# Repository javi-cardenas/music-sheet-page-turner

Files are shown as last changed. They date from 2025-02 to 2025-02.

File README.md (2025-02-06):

# Sheet Music Page Turner

This page-turning device was designed with reading and multitasking in mind. While devices for eBooks already exist, our solution primarily aimed to provide a cheaper hands-free alternative for physical sheet music books.

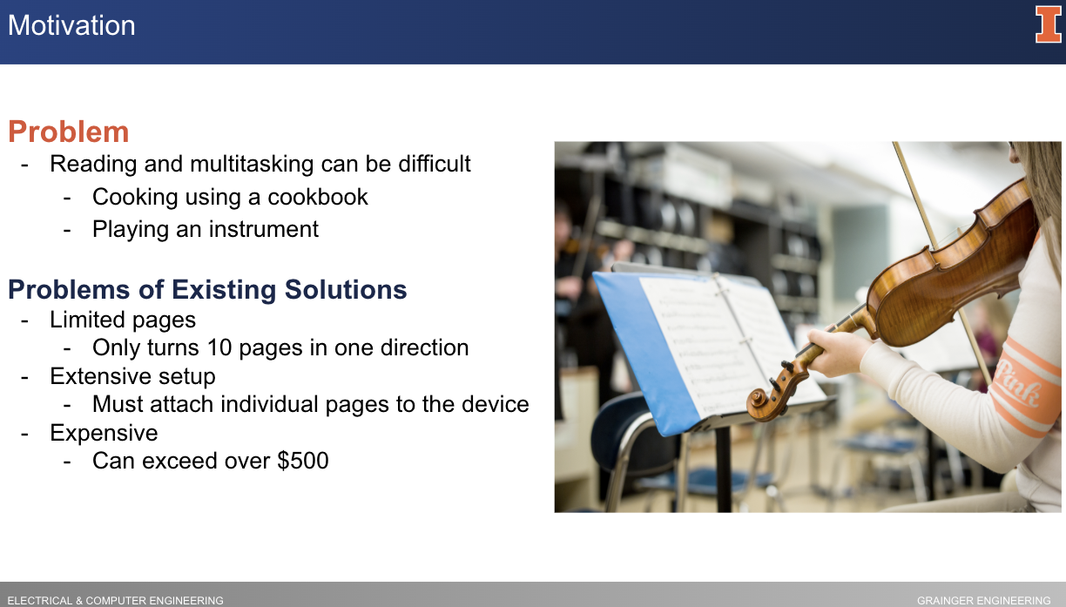
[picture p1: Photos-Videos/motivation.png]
Problem


<div align="center">
  <h2>Minimum Viable Product</h2>
</div>

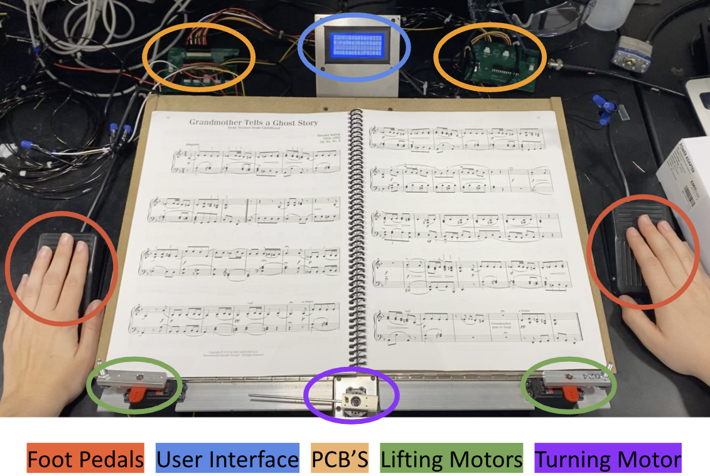
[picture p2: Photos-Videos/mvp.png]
Minimum Viable Product


Our page turner uses two foot pedals as input and three servo motors to turn pages forward or backward. The servo motors are attached to the base of a wooden stand and a liquid crystal display (LCD) is mounted to a metal enclosure.

Ultimately, the device was successfully able to turn pages in both directions, consecutively turn up to 10 pages in a row, and digitally track the number of pages the user turned.

**Note:** Feel free to take any inspiration, but this code was not intended to be cloned and deployed. As such, I do not provide support or guidance for this.

<div align="center">
  <h2>Software Flow Chart</h2>
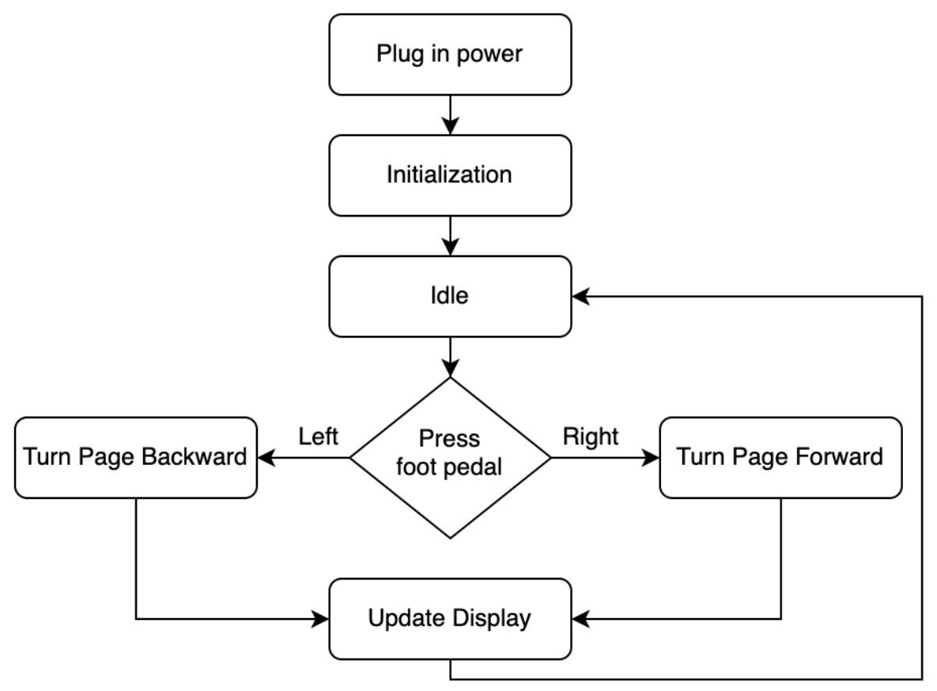
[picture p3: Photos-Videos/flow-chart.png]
Software Flow Chart
  
</div>

<div align="center">
  <h2>Block Diagram</h2>
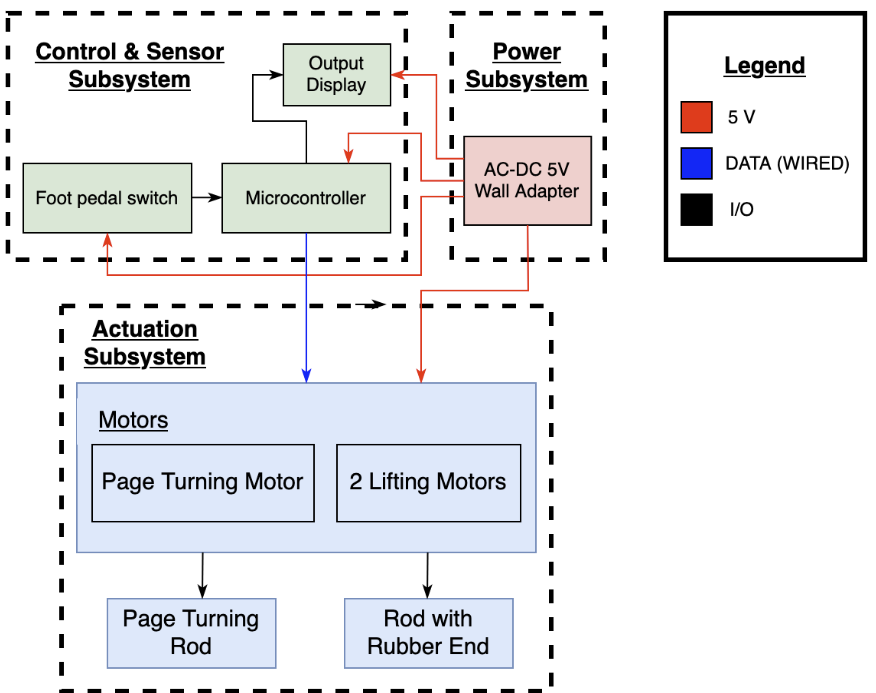
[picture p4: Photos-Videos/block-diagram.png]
Block Diagram
  
</div>

<div align="center">
  <h2>Circuit Schematic</h2>
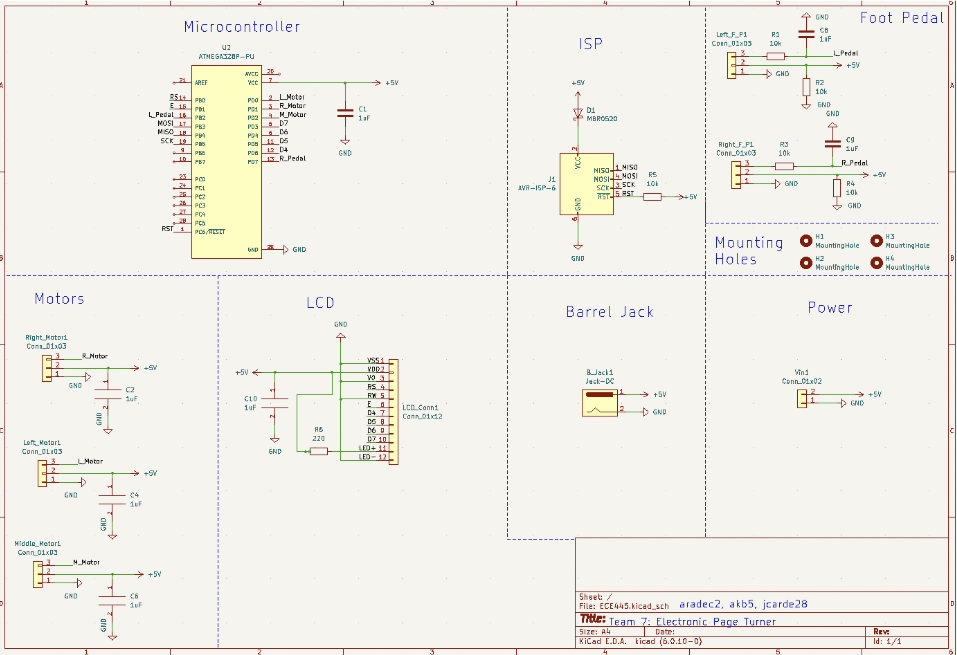
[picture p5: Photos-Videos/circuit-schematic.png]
Circuit Schematic
  
</div>

<div align="center">
  <h2>Printable Circuit Board (PCB) Diagram</h2>
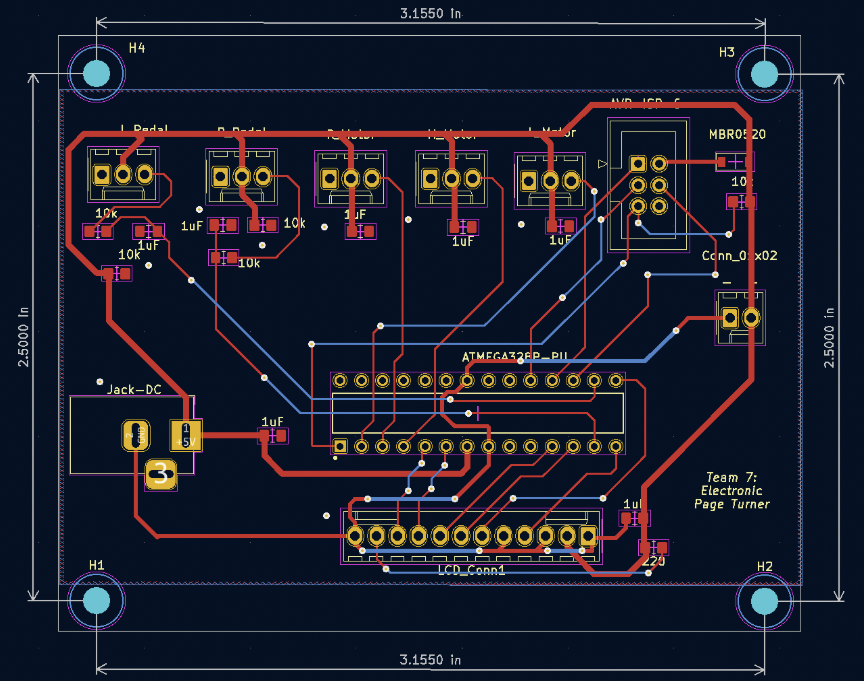
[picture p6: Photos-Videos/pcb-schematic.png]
Printable Circuit Board (PCB) Diagram
  
</div>

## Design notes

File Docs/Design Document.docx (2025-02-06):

ECE 445 Senior Design

Design Document

Electronic Page Turner

Team No. 7

Adia Radecka

(aradec2@illinois.edu)

Alyssa Bradshaw

(akb5@illinois.edu)

Javi Cardenas

(jcarde28@illinois.edu)

TA: Raman Singh

Professor: Viktor Gruev

March 31, 2023

Table of Contents

1. Introduction 2

1.1 Problem 2

1.2 Solution 3

1.3 High-Level Requirements 3

2. Design 6

2.1 Block Diagram 6

2.2 Subsystem Overview 6

2.2.1 Power Subsystem 6

2.2.2 Control & Sensor Subsystem 7

2.2.3 Actuation Subsystem 8

2.3 Subsystem Requirements 9

2.2.1 Power Subsystem 9

2.2.2 Control & Sensor Subsystem 9

2.2.3 Actuation Subsystem 9

2.4 Tolerance Analysis 9

3. Cost & Schedule 10

3.1 Cost Analysis 10

3.2 Schedule 11

4. Ethics & Safety 13

4.1 Ethics 13

4.2 Safety 13

5. References 14

# 1. Introduction

## 1.1 Problem

When reading a book, manual page-turning is a crucial requirement. This simple task can inconvenience those wishing to multitask while reading. A prime example occurs when a musician must stop playing their instrument to turn the sheet music when practicing or performing music. Another example is when cooking and using a cookbook; one may not have free or clean hands to turn the pages. Furthermore, a group to consider is those with disabilities who cannot physically turn a book's pages [1]. These are just a few examples of electronic page-turners’ usefulness, but not many exist. Those that do are generally expensive and typically designed for electronic tablet reading. Another issue with existing page-turners for physical books is that they are made for a limited number of pages and can only turn them in one direction. They also require a lengthy setup to attach each page to the device, which is an issue for those wanting to use a book with more pages than the device can handle.

## 1.2 Solution

To solve this problem, our team aims to create a hands-free electronic page-turner that functions with a foot pedal. The device uses two foot pedal switches to turn a page forward or backward. When the foot pedal is pressed, the control system communicates with the motors to start turning a page. A rubber tip attached to the end of a motor is used to lift a single page at a time. A rod connected to another motor will sweep underneath the raised page, causing it to turn to the next page. Our solution is unique because the device does not require extensive setup and can go through all the pages in a physical book in both directions.

## 1.3 Visual Aid

We provide a pictorial representation of our solution in Figure 1. The main components attached to the book stand will be the motors and a Liquid Crystal Display (LCD).

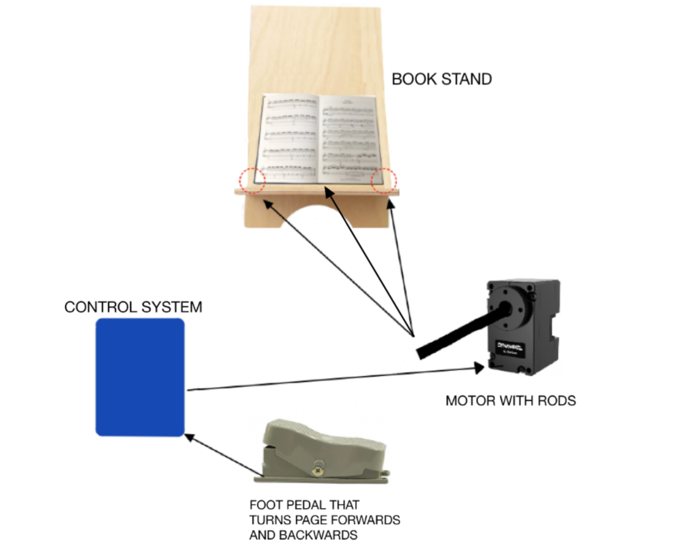
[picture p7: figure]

Figure 1: Visual Aid

## 1.4 High-Level Requirements

For our solution to be considered successful, it must achieve the following three goals:

- The device must be able to turn one page within 5 seconds ± 2 seconds. This motion should be repeatable for turning a page backward.
- The device must be able to turn at least ten consecutive pages, with 95% ± 5% accuracy, and take at most 1 minute ± 10 seconds when the foot pedal is pressed consecutively.
- The device must be able to store the total number of pages turned in a single sitting, with 95% ± 5% accuracy, and display this information to the reader.

# 2. Design

## 2.1 Physical Design

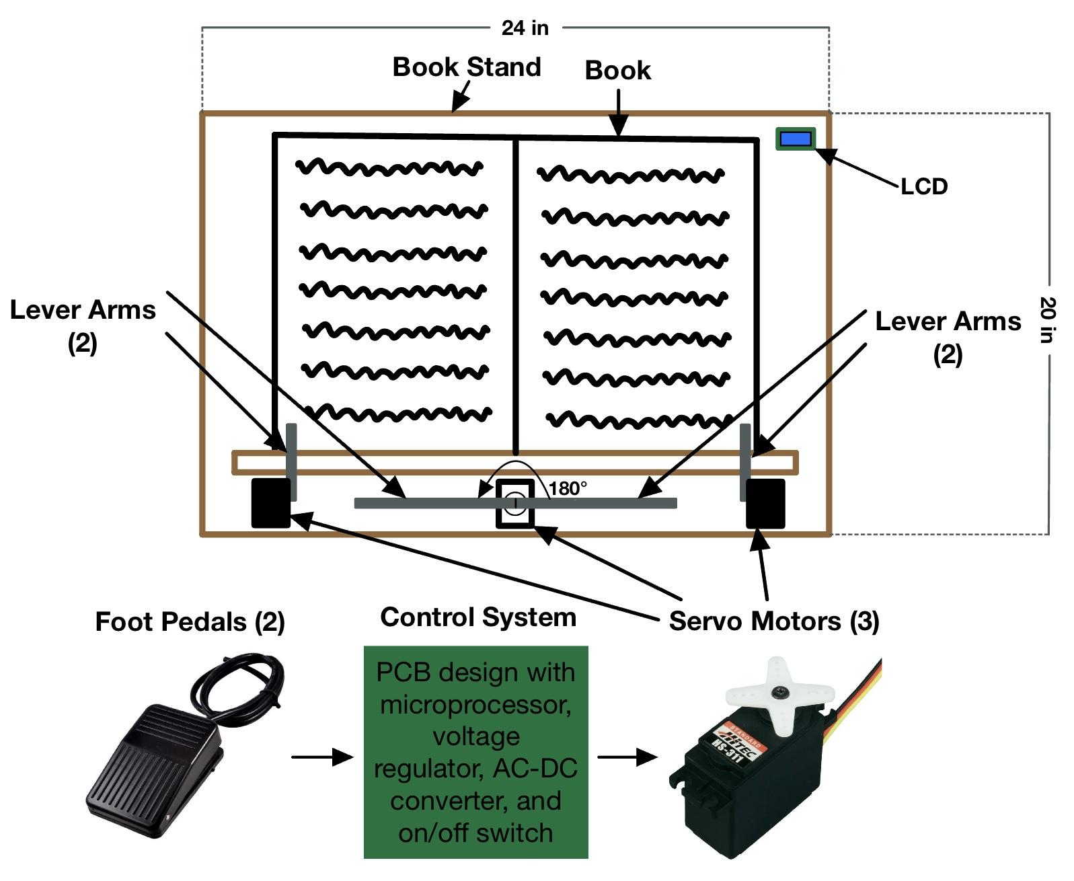
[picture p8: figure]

Figure 2: Physical Design

This physical design consists of two foot pedal switches, three servo motors, a physical stand to hold the book, a PCB, and an LCD. The input to our device is two foot pedals, and the physical page-turning and LCD act as the output. The LCD keeps track of the number of pages turned forward. The system uses a 5V wall-power adapter to power all its components. The PCB comprises the microcontroller and headers to connect the pedals, motors, and LCD. Two servo motors with rods containing rubber tips at their ends must be located by the corners of the book stand to raise a single page vertically. The center servo motor includes a long rod to sweep underneath the raised page.

## 2.2 Block Diagram

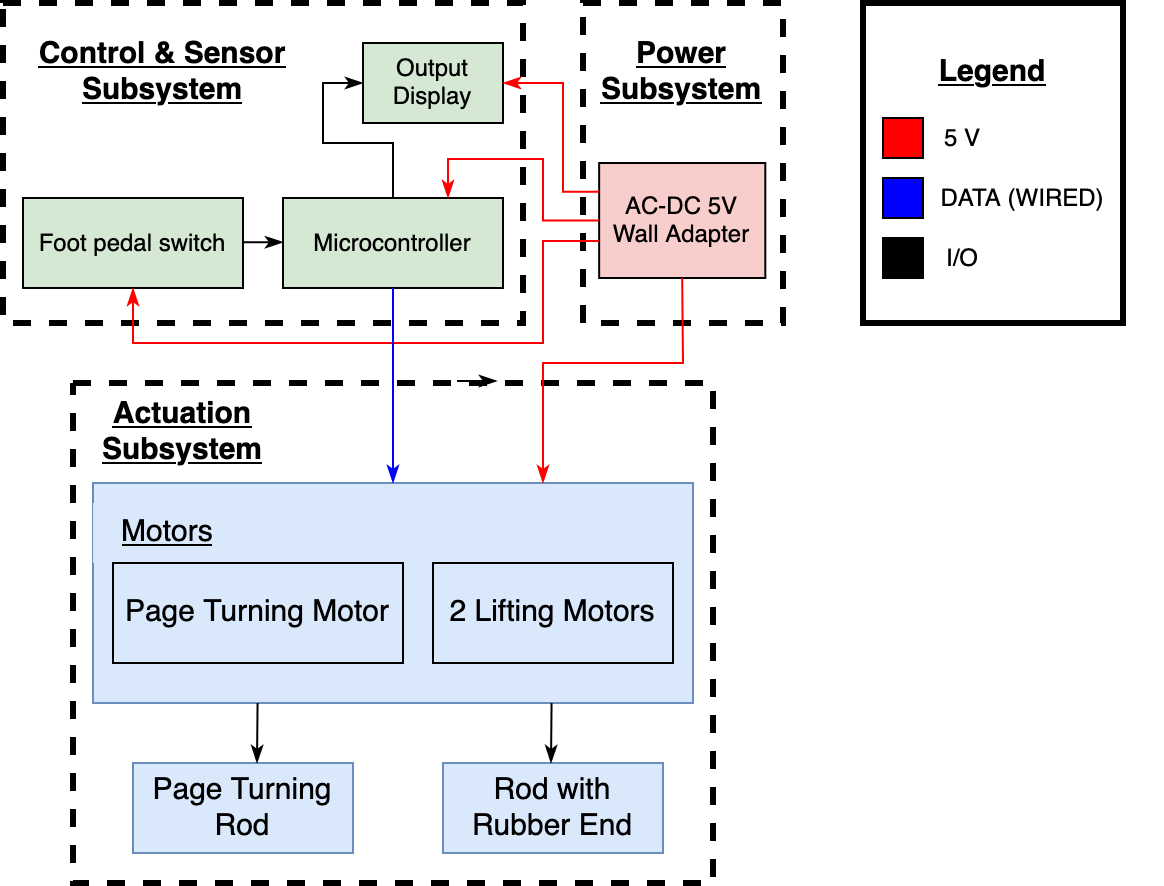
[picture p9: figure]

Figure 3: Block Diagram

## 2.3 Subsystem Overview

Our design is divided into three subsystems: Power, Control & Sensor, and Actuation subsystems.

### 2.3.1 Power Subsystem

The power subsystem handles sending power to the rest of the components in the other two subsystems. The power subsystem includes a 5V wall-power adapter that converts from AC-DC, supplying a steady 5V to the rest of the subsystems.

### 2.3.2 Control & Sensor Subsystem

The control and sensor subsystem contains the microcontroller and sensors needed to move the motors. This includes the ATMEGA328P microcontroller, two foot pedal switches, and an LCD. When a foot pedal is pressed, a signal is sent to the microcontroller, determining whether a page is turned forward or backward. The microcontroller then sends a signal to turn on the correct servo motors. The LCD keeps track of the number of pages turned forward.

### 2.3.3 Actuation Subsystem

Two servo motors will lift a single page vertically, the left and right pages, respectively. Attached to the end of each lifting motor will be a short rod with a rubber tip; these motors will be located at the bottom corners of each page. The remaining servo motor will turn the page forward or backward. This page-turning motor will be located by the center of the book stand. Attached to the page-turning motor will be a long rod that rests below the bottom of the book. When the foot pedal is pressed, and the microcontroller processes and sends the signal, the page-turning process will start. First, the lifting motor will move from 0° to 45°, next the center motor will move from 0° to 90°, then the lifting motor will return to its starting position, and finally, the center motor will move to 180° causing the raised page to turn to the next page.

## 2.4 Subsystem Requirements

The requirements for each of our subsystems.

### 2.4.1 Power Subsystem

The power subsystem handles sending power to the rest of the components in the other two subsystems.

Requirements | Verification
- Must have a 5V wall adapter that plugs into a wall outlet. - All components must be supplied with 5 V ± 5%, when the devices are idle and when active. | - Use a multimeter to check that the wall adapter’s barrel jack is supplying a steady 5V ± 5%. - While the device is turned on, measure the voltage across each device using an oscilloscope. Repeat this process when a foot pedal is pressed.

### 2.4.2 Control & Sensor Subsystem

The control and sensor subsystem contains the microcontroller and sensors needed to move the motors. The foot pedal sensor must be able to send a signal when pressed to the microcontroller. The microcontroller must then communicate with the motors to begin turning pages.

Requirements | Verification
- When the left foot pedal is pressed, the corresponding motors to turn a page backward should rotate. When the right foot pedal is pressed, the corresponding motors to turn a page forward should rotate. - LCD Display must track the number of pages turned forward. | - Test the situation where the foot pedal is not pressed. Ensure that the motors do not rotate. - Test the situation where the foot pedal is pressed. Ensure that the lifting motors rotate 0°-45°-0° and the center motor rotates 0°-90°-180°. - When a page is turned forward, the count should increase by 1. If a page is turned backward, the count should decrease by 1.

### 2.4.3 Actuation Subsystem

The actuation subsystem handles the mechanical work of turning the page and includes three servo motors. The motors must successfully lift a page and then turn that page over. This motion must be repeatable for forwards and backwards page turning.

Requirement | Verification

- The servo motors must create negligible backwards EMF.
- The force of the motors should not be enough to cause tearing or damage to the books pages.
- Use an oscilloscope to plot the voltage of a motor when idle and when active. If the voltage spike is 1V ± 0.5V we can consider the backwards EMF from the motor negligible. Otherwise, we will add more capacitors and diodes to prevent negatively impacting the other hardware in our device.
- Using a singular lifting motor, run 10 trials to test how the force and speed required to lift one page. Tune the parameters in software accordingly.
- Using the sweeping motor, run 10 trials to test the force and speed required to lift one page. Tune the parameters in software accordingly. The slowest speed required to turn a page will be chosen for safety.

## 2.5 Tolerance Analysis

A crucial part of our project's success is the motors to lift a single page and the center motor to flip the page. We must consider the thickness of a book and how far along into the book we are for the lifting motors to hold a page vertically. For testing, we will be using a music sheet book with the following dimensions: 9 x 0.24 x 12 inches. The lifting motors must reach low enough to grab the very last page of the book, which would be at 0.0025 inches. We determined that the page must be lifted one inch to provide the sweeping rod attached to the center motor enough space to flip the page. Therefore a singular page must be displaced 45°, with respect to, the book if using a one inch rod to lift the page as shown in Equation 1.

Θ_(page, max) =tan^(-1) (1/1)=45°=0.785 rad

Equation 1: Angular displacement for a 1 in. rod attached to lifting motor

Θ_(page, min) =tan^(-1) (1/3)=18.4°=0.321 rad

Equation 2: Angular displacement for a 3 in. rod attached to lifting motor

Θ_(sweep) =180°=3.14 rad

Equation 3: Angular displacement for sweeping rod attached to center motor

Additionally, two of our high-level requirements involve time. More specifically, the time it takes to flip a single page and to turn ten pages consecutively. According to the datasheet for the motors, the maximum torque each can provide is 5.5 kg/cm = 0.053937 Nm, as shown in Equation 4. Ideally, each motor will receive 600 mW of power, as shown in Equation 5. By finding the maximum angular velocity, in Equation 6, the time it takes for each motor to complete its angular displacement can be calculated as shown in Equation 7. This process will ideally take 423.62 ms (2 X 70.603 + 282.41 ms). While these calculations are under ideal conditions, realistically, we can expect the process to take about 1 second. We also have to consider going too fast may cause physical damage to the book’s pages, which we plan to avoid. Furthermore, the time delay for signals from the foot pedal and microcontroller will require additional time. Therefore our given estimate in the high-level requirements is a reasonable baseline.

τ_(motor) =5.5 kg/cm = 0.053937 Nm

Equation 4: Maximum torque provided in motor datasheet

P_(motor) =I_(motor) V_(motor)

P_(motor) =0.1 [A] ×6 [V] = 0.6 W

Equation 5: Maximum power provided to each motor

P=τω→ω = P÷τ

ω=0.6 [W] ÷0.053937 [Nm] = 11.124 rad/s

Equation 6: Maximum angular velocity for each motor

t_(Θ_(page, max)) = (1 s)/(11.124 rad)×0.785 rad =70.603 ms

t_(Θ_(page, min)) = (1 s)/(11.124 rad)×0.321 rad =28.924 ms

t_(Θ_(sweep)) = (1 s)/(11.124 rad)×3.14 rad =282.41 ms

Equation 7: Time required for each motor to reach their angular displacement

# 3. Cost & Schedule

## 3.1 Cost Analysis

Production of this device is estimated at 30 hours per week over 15 weeks distributed amongst three people. The three of us are electrical engineering majors, and based on our current job offers, the average pay is $40 per hour. Based on this hourly rate, the estimated labor cost for this initial design is $18,000.

Below we have included a table to breakdown the cost of all parts required for the initial design. Based on these numbers we estimate a cost of $129.57 for all required components.

Part | Part Number | Unit Price | Quantity | Total
Microcontroller | ATMEGA328P-PU | | 1
Foot Pedal | n/a | $10.43 | 2 | $20.86
Servo Motor | HS-311 | $14.76 | 3 | $44.28
PCB Manufacture | n/a | $30.00 | 1 | $30.00
On/Off Switch | JS202011CQN | $0.60 | 1 | $0.60
AC to DC Converter | UCC28610DR | $1.65 | 1 | $1.65
Barrel Jack | PJ-102AH | $0.82 | 1 | $0.82
Power Plug | PP3-002A | $1.44 | 1 | $1.44
Linear Regulator | LM117MP | $1.70 | 1 | $1.69
ISP Header | 1597-114020164-ND | $2.80 | 1 | $2.80
3 Pin Header | WM4201-ND | $0.27 | 3 | $0.81
LCD Display | 2632-C162A-BW-LW65-ND | $6.27 | 1 | $6.27
10k Resistor | 2197-294-10-RC-ND | $0.15 | 3 | $0.45
1uF Capacitor | 478-1836-ND | $0.82 | 3 | $2.46
3 pin MTA100 connector | A19470-ND | $0.23 | 3 | $0.69
3D Printed Motor Rods | N/a | $1.00 | 3 | $3.00
Total Cost | | | | $129.57

Table 1: Total Cost of Required Components

## 3.2 Schedule

- Week of 02/20; Week 6

Design Document, Team Contract, Revise Proposal, Work on PCB Design in office hours, Make design review presentation

- Week of 02/27; Week 7

Design Review, PCB Review, pickup stand built by Machine shop, Continue working on PCB design, Pickup all ordered parts

- Week of 03/06; Week 8

First round PCB orders, Order PCB parts, Order PCB, Teamwork Evaluation

- Week of 03/13; Week 9

Spring Break

- Week of 03/20; Week 10

Prototype 1: Solder PCB, Put all mechanical and electrical parts together, debug and review

- Week of 03/27; Week 11

Order second PCB if needed, Individual Evaluation, Debug Review

- Week 0f 04/03; Week 12

Prototype 2: Debug and review

- Week of 04/10; Week 13

Team contract fulfillment

- Week of 04/17; Week 14

Mock Demo, review, work on Final Demo and presentation

- Week of 04/24; Week 15

Final Demo, Mock Presentation, work on presentation and paper

- Week of 05/01; Week 16

Final Presentation, Final Paper

# 4. Ethics & Safety

## 4.1 Ethics

The IEEE code of ethics lists a few policies that should be considered while working on this project. Policy 1.5 states “to seek, accept, and offer honest criticism of technical work, to acknowledge and correct errors, to be honest and realistic in stating claims or estimates based on available data, and to properly credit the contributions of others''. [2] This policy applies to this project because page-turners are currently available. We will adequately credit any work done on page-turners and build upon those ideas. Additionally, criticism and new ideas will be welcomed so that our project development process is rewarding.

## 4.2 Safety

Although our project is a hands-free device, there is a possibility of injury if any bodily parts interfere with the device while it is in motion. The rods attached to the motors will perform a sweeping action to turn the pages. While there is not enough force to cause severe injury, placing your hand in the way while the rod is in motion may hurt. We need to keep in mind the rod's material and the speed of the motors so that if contact does occur, it will not cause any severe damage. Setting the correct speed is also important to avoid tearing or damage to the pages of the book. If the speed is too fast, the force of the rods can cause damage to the book. To prevent this from occurring, we plan to tune the parameters in the software accordingly. Ideally, the slowest speed that still turns a page will be chosen to avoid any safety issues. Also, if someone has their hands in the way and causes the motor to stall, this will cause the motor to heat up. Although unlikely, this could potentially cause a burn to the individual.

Another potential danger could be from the power subsystem. Although our device does not require high voltage to operate, we will use a wall power adapter which creates the issue of electric shock. Electric shock occurs when current flows through your body. The larger the voltage, the more current there is and the worse the shock could be. An electric shock can occur if you touch the live and neutral wire of the power supply as you become a part of the circuit and allow current to flow through you. It is essential to be mindful of this connection and not to touch the leads of these wires when plugged into the power supply. It is also crucial to ensure none of the equipment is faulty as this can cause electric shock. Faulty equipment includes but is not limited to damaged wires, damaged plugs, broken connections, wet plugs, and plugs with missing prongs[3]. Before using any equipment, our team will take the mandatory high voltage safety training and plan to keep this training in mind as we work on our project to avoid the danger of electric shock. We will also implement the one-hand rule to prevent current from flowing into your body and out the other connection point. We will also check to make sure all equipment is undamaged before use.

# 5. References

[1] “Assistive Technologies for Reading,”ASCD, Dec-2005. [Online]. Available: https://www.ascd.org/el/articles/assistive-technologies-for-reading. [Accessed:06-Feb-2023]

[2] “IEEE code of ethics,” IEEE, Jun-2020. [Online]. Available: https://www.ieee.org/about/corporate/governance/p7-8.html. [Accessed:06-Feb-2023].

[3] C. C. for O. H. and S. Government of Canada, “The Young Workers Zone : Teaching Tools : Physical hazards: Electrical,” The Young Workers Zone : Teaching Tools : Physical Hazards: Electrical, 12-Jul-2010. [Online]. Available: https://www.ccohs.ca/teach_tools/phys_hazards/electrical.html. [Accessed: 23-Feb-2023].

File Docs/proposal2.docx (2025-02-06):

ECE 445 Senior Design

Project Proposal

Electronic Page Turner

Team No. 7

Adia Radecka

(aradec2@illinois.edu)

Alyssa Bradshaw

(akb5@illinois.edu)

Javi Cardenas

(jcarde28@illinois.edu)

TA: Raman Singh

Professor: Viktor Gruev

February 9, 2023

Table of Contents

1. Introduction 2

1.1 Problem 2

1.2 Solution 2

1.3 Visual Aid 2

1.4 High-Level Requirements 3

2. Design 4

2.1 Block Diagram 4

2.2 Subsystem Overview 4

2.2.1 Power Subsystem 4

2.2.2 Control & Sensor Subsystem 5

2.2.3 Actuation Subsystem 5

2.3 Subsystem Requirements 5

2.2.1 Power Subsystem 5

2.2.2 Control & Sensor Subsystem 6

2.2.3 Actuation Subsystem 6

2.4 Tolerance Analysis 6

3. Ethics & Safety 9

3.1 Ethics 9

3.2 Safety 9

4. References 11

# 1 Introduction

## 1.1 Problem

When reading a book, manual page-turning is a key requirement. This can be an inconvenience for those wishing to multitask while reading. A prime example of this occurs when a musician has to stop playing their instrument in order to turn the sheet music when practicing or performing music. Another example is when cooking and using a cookbook, one may not have free or clean hands to turn the pages. Furthermore, a group to consider is those with disabilities who are unable to physically turn a book's pages [1]. There are a number of examples supporting the usefulness of electronic page turners, but not many exist. Those that do are generally expensive and are typically designed for electronic reading on tablets. Another issue with existing page turners for physical books is that they are made for a limited number of pages and can only turn the pages in one direction. They also require lengthy setup to attach each page to the device. This is an issue for those wanting to use a book with more pages than the device can handle.

## 1.2 Solution

To solve this problem, our team aims to create a hands-free electronic page turner that functions with a foot pedal. The device will use a dual switch foot pedal such that a page can be turned in both directions. When the foot pedal is pressed, the control system communicates to the motors to begin turning a page. A paper safe adhesive, attached to a motor, will be used to lift up a single page at a time. Next, the page will be turned over by a rod sweeping underneath. This system and motion will be reused for turning a page both forwards and backwards. Additionally, the device will be powered using batteries so that the device can be made as portable as possible. Our solution is unique because the device does not require extensive setup and can turn through all the pages in a physical book, both forwards and backwards.

## 1.3 Visual Aid

We provide a pictorial representation of our solution in Figure 1. The primary components such as the motors will be attached to a book stand.


Figure 1: Visual Aid

## 1.4 High-Level Requirements

For our solution to be considered successful, it must achieve the following three goals.

If the team is able to accomplish all three high level requirements, we aim to produce prototypes that can turn a page by using additional sensors.

- The device must be able to turn one page within 5 seconds ± 2 seconds. This motion should be repeatable for turning a page backwards.
- The device must be able to turn at least 10 consecutive pages with 95% ± 5% accuracy and take at most 1 minute ± 10 seconds when the foot pedal is pressed consecutively.
- The device must be able to store the total number of pages turned, in a singular sitting, with 95% ± 5% accuracy and display this information to the reader.

# 2 Design

## 2.1 Block Diagram

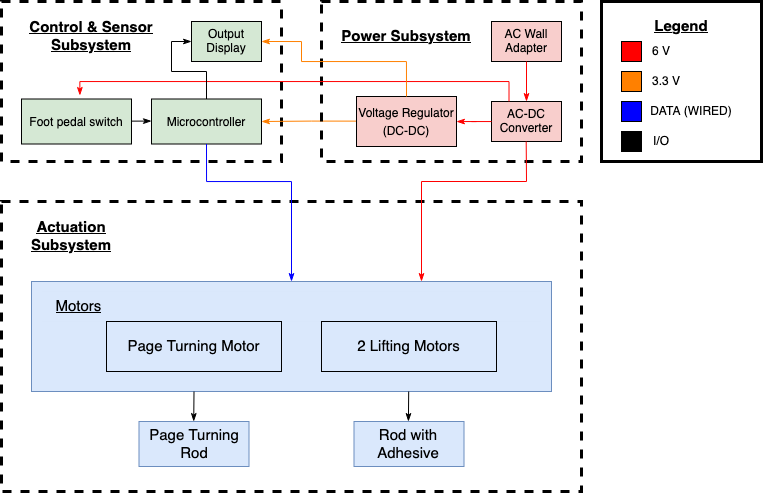
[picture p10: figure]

Figure 2: Block Diagram

## 2.2 Subsystem Overview

Our design is divided into three subsystems: Power, Control & Sensor, and Actuation subsystems.

### 2.2.1 Power Subsystem

The power subsystem handles sending power to the rest of the components in the other two subsystems. The power subsystem includes an AC wall adapter, an AC-DC converter that should supply 6 V, a DC to DC voltage regulator, and an On/Off switch. The voltage regulator reduces the voltage needed to power the foot pedal and microcontroller.

### 2.2.2 Control & Sensor Subsystem

The control and sensor subsystem contains the microcontroller and sensors needed to move the motors. This primarily includes the Arduino Nano 33 BLE Sense and dual switch foot pedal. When the foot pedal is pressed a signal is sent to the microcontroller which determines whether a page is turned forward or backwards. The microcontroller then sends a signal to turn on the correct servo motors. Any additional sensors such as a microphone and camera will be included here as well.

### 2.2.3 Actuation Subsystem

The actuation subsystem handles the mechanical work of turning the page and includes three servo motors. Two servo motors will be used for lifting a single page, the left and right page respectively. Attached to each lifting motor will be a short rod with paper safe adhesive attached to the end. The shorter rods will be located at the bottom corners of each page. The remaining servo motor will be used for turning the page forward or backwards. This page turning motor will be located near the center of the book stand. Attached to the page turning motor will be a long swiping rod that rests below the bottom of the book. In its entirety, when the foot pedal is pressed, and the microcontroller processes and sends the signal, the lifting motor will lift the current page using the attached adhesive. The page turning motor will then turn on and sweep beneath the current page, turning it over to the next page.

## 2.3 Subsystem Requirements

The requirements for each of our subsystems.

### 2.2.1 Power Subsystem

The power subsystem handles sending power to the rest of the components in the other two subsystems.

Requirements | Verification
- Must have a 6V wall adapter that plugs into a wall outlet. - Must have an AC-DC converter. - Must have a voltage regulator to supply 3.3V. - Motors must be supplied 6V and 100mA each. | - Use a multimeter to check that the wall adapter’s barrel jack is supplying a steady 6V. - Use an oscilloscope to measure the output of the AC-DC converter to make sure it is consistently 6V. - Use an oscilloscope to measure the output of the voltage regulator to make sure it is consistently 3.3V. - Power the motors using a 6V power supply and use an oscilloscope to plot the current and voltage across the motors power wire.

### 2.2.2 Control & Sensor Subsystem

The control and sensor subsystem contains the microcontroller and sensors needed to move the motors. The foot pedal sensor must be able to send a signal when pressed to the microcontroller. The microcontroller must then communicate with the motors to begin turning pages.

Requirements | Verification
- When the foot pedal sensor is pressed, it must send a signal to the microcontroller. The microcontroller must then send a signal to the motors that causes them to rotate. | - Program the foot pedal and a motor using an Arduino Nano 33 BLE Sense development kit. - Test the situation where the foot pedal is not pressed. Ensure that the motor does not rotate. - Test the situation where the foot pedal is pressed. Ensure that the motor rotates 45° and 180°. - Time the process to rotate the motors 45° and 180° respectfully. Make sure on average the entire process is done within 3 seconds ± 2 seconds.

### 2.2.3 Actuation Subsystem

The actuation subsystem handles the mechanical work of turning the page and includes three servo motors. The motors must successfully lift a page and then turn that page over. This motion must be repeatable for forwards and backwards page turning.

Requirement | Verification

- The rods attached to the lifting motors must successfully lift a page 1 in. vertically, using adhesive.
- The motors must be able to turn a page forwards and backwards.
- The servo motors must create negligible backwards EMF.
- The force of the motors should not be enough to cause tearing or damage to the books pages.
- Run 10 trials to see how much adhesive is needed to lift the page 1 in. vertically.
- Using a singular lifting motor, run 10 trials to test how much force is required from the motors to lift one page. Tune the parameters in software accordingly.
- Using the sweeping motor, run 10 trials to test how much force is required from the motors to lift a one page. Tune the parameters in software accordingly. Ideally, the slowest speed that still turns a page will be chosen to avoid any safety issues.
- Power the motor using a 6V power supply and use an oscilloscope to plot the voltage across the motors power wire. If the voltage across the wire is on average 100mV ± 50mV we can consider the backwards EMF from the motor negligible.
- Adjusting the rod distance from the page to fluctuate force applied, run 10 trials that successfully cause no damage to the book.

## 2.4 Tolerance Analysis

A key part of our project to be successful are the motors to lift up a single page and the center motor to flip the page. We must take into account the thickness of a book and how far along into the book we are for the lifting motors to successfully hold a page vertically. For testing we will be using a music sheet book with the following dimensions: 9 x 0.24 x 12 inches. The lifting motors must be able to reach low enough so that they can grab the very last page of the book, which would be at a height of 0.0025 inches. We determined that the page must be lifted up 1 inch to provide the sweeping rod attached to the center motor enough space to flip the page. This means a singular page must be displaced 45° with respect to the book, if using a 1 in. rod to lift the page as shown in Equation 1.

Θ_(page, max) =tan^(-1) (1/1)=45°=0.785 rad

Equation 1: Angular displacement for a 1 in. rod attached to lifting motor

Θ_(page, min) =tan^(-1) (1/3)=18.4°=0.321 rad

Equation 2: Angular displacement for a 3 in. rod attached to lifting motor

Θ_(sweep) =180°=3.14 rad

Equation 3: Angular displacement for sweeping rod attached to center motor

Additionally, two of our high level requirements involve time. More specifically the time it takes to flip a single page and the time to flip 10 pages consecutively. According to the datasheet for the motors, the maximum torque each one of these can provide is 5.5 kg/cm = 0.053937 Nm as shown in Equation 4. Ideally, each motor will receive 600 mW of power, as shown in Equation 5. By finding the maximum angular velocity, Equation 6, the time it takes for each motor to complete its angular displacement can be calculated as shown in Equation 7. In its entirety, this process will ideally take 423.62 ms (2 X 70.603 + 282.41 ms). While these calculations are under ideal conditions, in reality we can probably expect this entire process to take about 1 second to complete. We also have to consider going too fast may cause physical damage to the book’s pages, which we plan to avoid. Furthermore, the time delay for signals from the foot pedal and microcontroller will require additional time. Therefore our given estimate in the high level requirements is a reasonable baseline.

τ_(motor) =5.5 kg/cm = 0.053937 Nm

Equation 4: Maximum torque provided in motor datasheet

P_(motor) =I_(motor) V_(motor)

P_(motor) =0.1 [A] ×6 [V] = 0.6 W

Equation 5: Maximum power provided to each motor

P=τω→ω = P÷τ

ω=0.6 [W] ÷0.053937 [Nm] = 11.124 rad/s

Equation 6: Maximum angular velocity for each motor

t_(Θ_(page, max)) = (1 s)/(11.124 rad)×0.785 rad =70.603 ms

t_(Θ_(page, min)) = (1 s)/(11.124 rad)×0.321 rad =28.924 ms

t_(Θ_(sweep)) = (1 s)/(11.124 rad)×3.14 rad =282.41 ms

Equation 7: Time required for each motor to reach their angular displacement

# 3 Ethics & Safety

## 3.1 Ethics

The IEEE code of ethics lists a few policies that should be kept in mind while working on this project. Policy 1.5 states “to seek, accept, and offer honest criticism of technical work, to acknowledge and correct errors, to be honest and realistic in stating claims or estimates based on available data, and to properly credit the contributions of others''. [2] This policy applies to this project because there are currently page turners available on the market. We will properly credit any work done on page turners and build upon those ideas. Additionally, criticism and new ideas will be welcomed so that our project development process is rewarding.

## 3.2 Safety

Although our project is a hands-free device, there is a possibility of injury if any bodily parts interfere with the device while it is in motion. The rods attached to the motors will perform a sweeping motion to turn the pages. While not enough force to cause very serious injury, placing your hand in the way while the rod is in motion may hurt. We need to keep in mind the material of the rods and the speed of the motors so that if contact does occur it will not cause any serious damage. Also, if someone has their hands in the way and causes the motor to stall, this will cause the motor to heat up. Although unlikely, this could potentially cause a burn to the individual. Because of this, we will need to be mindful of when the system is in use so that all hands are out of the way and the motors can move freely.

Another potential danger could be from the power subsystem. Although our device does not require high voltage to operate, we will be using a wall power adapter which will require us to step down from 120 volts to 6 volts. This will cause high heat dissipation which can cause harm to the user. To minimize the heat dissipation, we plan to use a switching regulator. The use of high voltage also presents the issue of electric shock. Electric shock occurs when current flows through your body. The higher the voltage being used, the more current there is and the worse the shock could be. An electric shock can occur if you touch the live and neutral wire of the power supply as you become a part of the circuit and allow current to flow through you. It is important to be mindful of this connection and to not touch the leads of these wires when plugged into the power supply. It is also important to make sure none of your equipment is faulty as this can also cause electric shock. Faulty equipment includes but is not limited to damaged wires, damaged plugs, broken connections, wet plugs, and plugs with missing prongs[3]. Before using any equipment our team will take the mandatory high voltage safety training and plan to keep this training in mind as we work on our project to avoid the danger of electric shock. We will also implement the one-hand rule as this will prevent current from flowing into your body and out the other connection point. We will also check to make sure all equipment is undamaged before use.

# References

[1] “Assistive Technologies for Reading,”ASCD, Dec-2005. [Online]. Available: https://www.ascd.org/el/articles/assistive-technologies-for-reading. [Accessed:06-Feb-2023]

[2] “IEEE code of ethics,” IEEE, Jun-2020. [Online]. Available: https://www.ieee.org/about/corporate/governance/p7-8.html. [Accessed:06-Feb-2023].

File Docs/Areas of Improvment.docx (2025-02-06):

- Adding a reset button so that if the middle motor jams, a reset button can be pressed to send it back to home
- For the bookmark, we should’ve used a keypad to type in the starting page number

Component | Mean Idle Voltage (V) | Mean Active Voltage (V)
Power Adapter | 5.215 | 5.185
Left Motor | 5.215 | 5.175
Center Motor | 5.140 | 5.120
Right Motor | 5.130 | 5.130
Microcontroller | 5.200 | 5.150
Left Foot Pedal | 5.200 | 5.170
Right Foot Pedal | 5.145 | 5.135
Liquid Crystal Display (LCD) | 5.200 | 5.140

Sometimes the system experiences a voltage drop, when idle and moving, around 800 mV. The first time testing this did not occur, but it did the second time. This could be due to the wiring we used to connect the oscilloscope probes. Either way it is less than a volt so the backward EMF is negligible.

Sampling Rate: 500 MS/s

Left Motor

Idle: 5.33 (max), 5.10(min)

Moving: 5.30 (max), 5.05 (min)

Middle Motor

Idle: 5.25 (max), 5.03 (min)

Moving: 5.23 (max), 5.01 (min)

Power Plug

Idle: 5.33 (max), 5.10 (min)

Moving: 5.31 (max), 5.06(min)

Left Foot Pedal:

Idle: 5.31(max), 5.09(min)

Moving: 5.29 (max), 5.05(min)

Right Motor:

Idle: 5.25 (max), 5.01(min)

Moving: 5.25 (max), 5.01(min)

Right Foot Pedal:

Idle: 5.28 (max), 5.01(min)

Moving: 5.26 (max), 5.01(min)

LCD:

Idle: 5.38 (max), 5.02(min)

Moving: 5.26 (max), 5.02(min)

4/24/23 Testing Videos Needed

- Oscilloscope testing setup for one component (take picture)
- Video pressing switches to to read LCD changes
- Video Turning one page forward and back (must be 10 seconds)
- Cut Original video to 1 min + 10 sec
- Take video with multimeter of Uconn

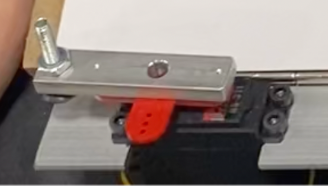
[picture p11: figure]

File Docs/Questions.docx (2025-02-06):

Weekly Meeting Questions

1. PCB Questions
  a. Can we use analog pins and digital pins on the microcontroller? We have 11 input/outputs
    i. 2 pedals, 3 motors, and possibly 6 for LCD
  b. Which jack component for the wall adapter on the PCB?
  c. Do we need a voltage regulator if we can use 5v for everything?
  d. Where do we need decoupling capacitors? Just by the microcontroller?
2. Design Document due Feb 23 11:59 PM
  a. Question about Physical Design, what is the difference between this and the visual aid?
3. Proposal Revisions due Feb 24 11:59 PM
  a. Clarification on comments a and c, should we remove component specifications in c?
4. Team Contract due Feb 24 11:59 PM
  a. Check our team contract
5. Anything else
  a. First-round and second-round pcb orders? What is this and does this mean we have 2 chances to submit?

Office Hour Questions

1. What has to be on the pcb? How much can be done by an arduino?
  a. Microcontroller subsystem
  b. Voltage regulator
  c. On/Off switch
  d. Foot pedals
2. PCB cost?

Motors and microcontroller

ISR capabilities specifically

AVR chip is nice, read datasheet

Everything has to go to the pcb by the end: sensors, microcontroller, and buttons

AC to DC converter - be wary about the barrel connector

Motor - 6V

Microcontroller - 3.3 or 5V

Foot pedal - have to test possible all 12

Linear Regulator - LM117

theta Ja is provided in datasheet

Paper calculation for overheating

Buck converter for motors

Integrated devices for buck converter

https://www.youtube.com/watch?v=a1DvWeJfzk4

https://www.resna.org/sites/default/files/legacy/conference/proceedings/2004/Papers/StudentDesign/OTH/PageTurner.html

https://courses.engr.illinois.edu/ece445/getfile.asp?id=19490

https://courses.engr.illinois.edu/ece445/getfile.asp?id=19775

https://courses.engr.illinois.edu/ece445/getfile.asp?id=19488

https://www.youtube.com/watch?v=mxqxxQXVkts

https://www.youtube.com/watch?v=ygrsIqWOh3Y

https://www.resna.org/sites/default/files/legacy/conference/proceedings/2003/Papers/SDwinners/Bailey2_TSP.htm

https://www.youtube.com/watch?v=dOa3570JM2M

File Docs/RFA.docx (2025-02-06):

Electronic Page Turner

Team Members:

- Javi Cardenas (jcarde28)
- Adia Radecka (aradec2)
- Alyssa Bradshaw (akb5)

Problem:

Page turning is required when reading a book. This is typically done with one's hands, which can be an inconvenience for those wishing to multitask while reading, such as playing an instrument or using a cookbook while cooking. This is a challenge for both avid readers and people with disabilities. There are hands-free page turners that exist, but most are expensive and typically designed for electronic reading on tablets.

Solution:

The solution for this problem will use three different subsystems: actuation, sensors, and power. Our solution is unique because it is a hands free page turner for a physical book that can turn an unlimited number of pages.

Actuation Subsystem:

1) Stand with a Lever/Arm
  a) This would be controlled by servo motors to turn the pages
  b) Two would be needed to flip pages forward and backwards
  c) Adjustable levers to accommodate different sized books

Power Subsystem:

1) Uses batteries to power required subsystems and allow for portability

Sensor Subsystem:

1) Button (easy)
  a) Using a foot pedal to turn the page forward and backwards

If we are able to meet the minimum requirements for success, we will try to implement the following:

2) Audio (medium)
  a) Using a microphone to turn pages forward when “Next” is said and backwards when “Back” is said
3) Vision (hard)
  a) Computer vision would be used alongside a camera to flip the page. It would be placed on the bottom left and right corners near the book and use some sort of facial cue in order to turn the page.

If we are able to meet the minimum requirements for success, we will try to implement the following:

Processing Subsystem:

1) A screen that displays the total pages flipped and how many pages were flipped in one sitting. This can help bookmark where you left off.
2) Include a timer to keep track of how much time you have read i.e. if someone wants to read for 30 mins the device can make a sound letting the user know the time is up.

Criterion for Success:

1) A stand for the book with levers for turning pages in the book
2) Has to be able to flip one page at a time, forward and backward
3) Should be able to go through all the pages in a book
4) Must be able to flip the pages using a foot pedal

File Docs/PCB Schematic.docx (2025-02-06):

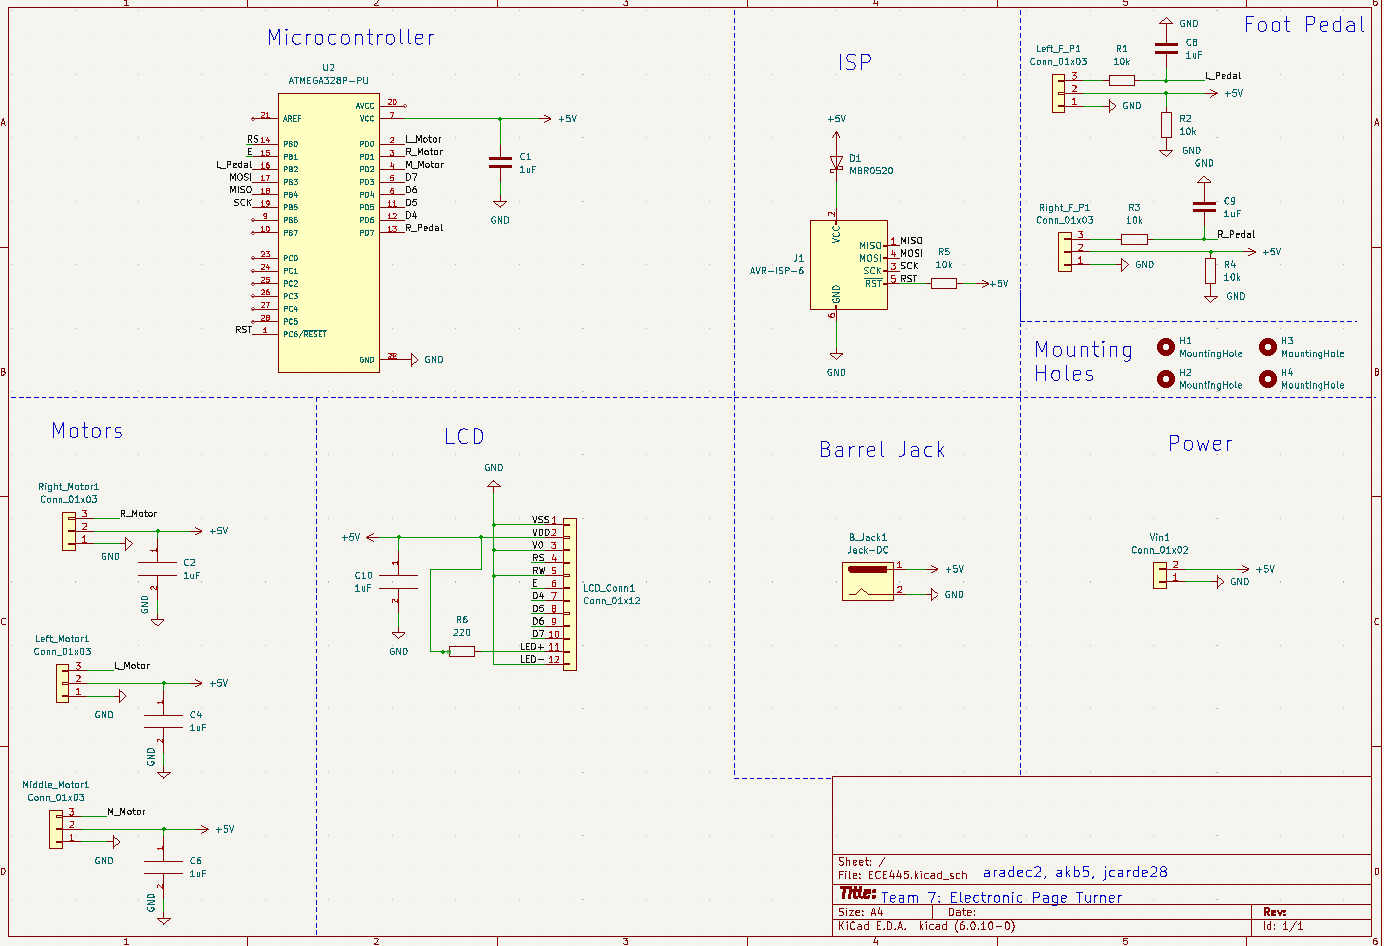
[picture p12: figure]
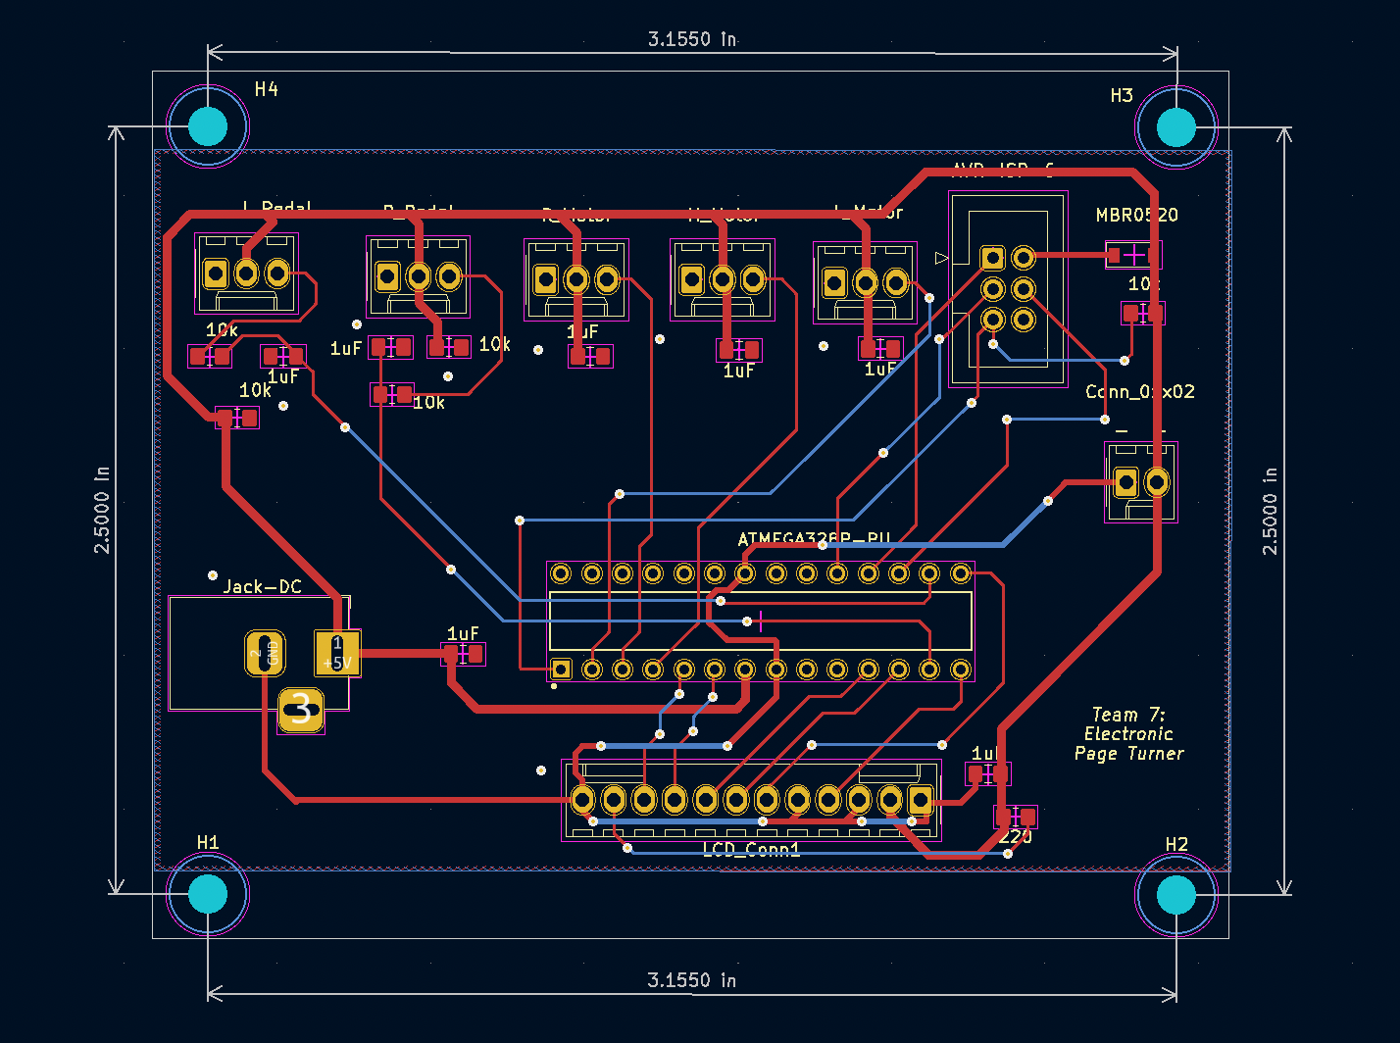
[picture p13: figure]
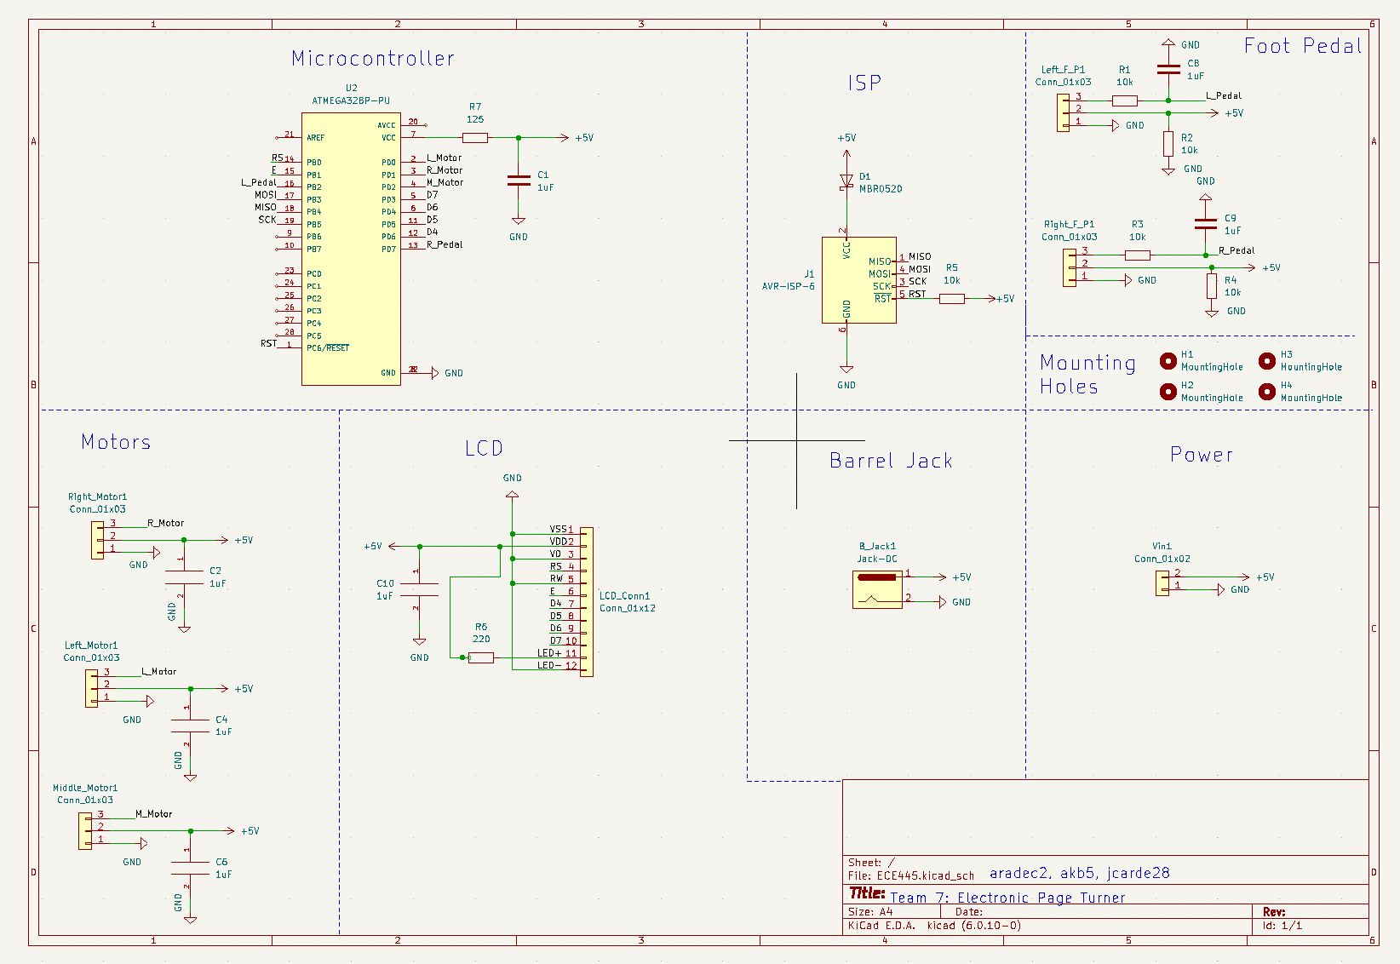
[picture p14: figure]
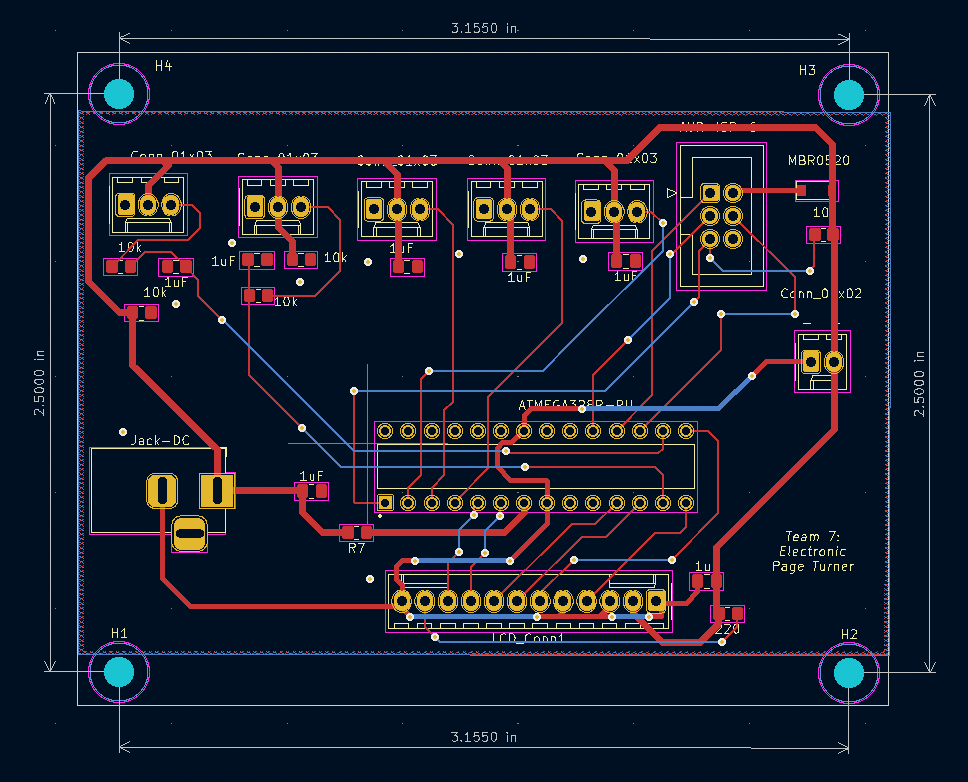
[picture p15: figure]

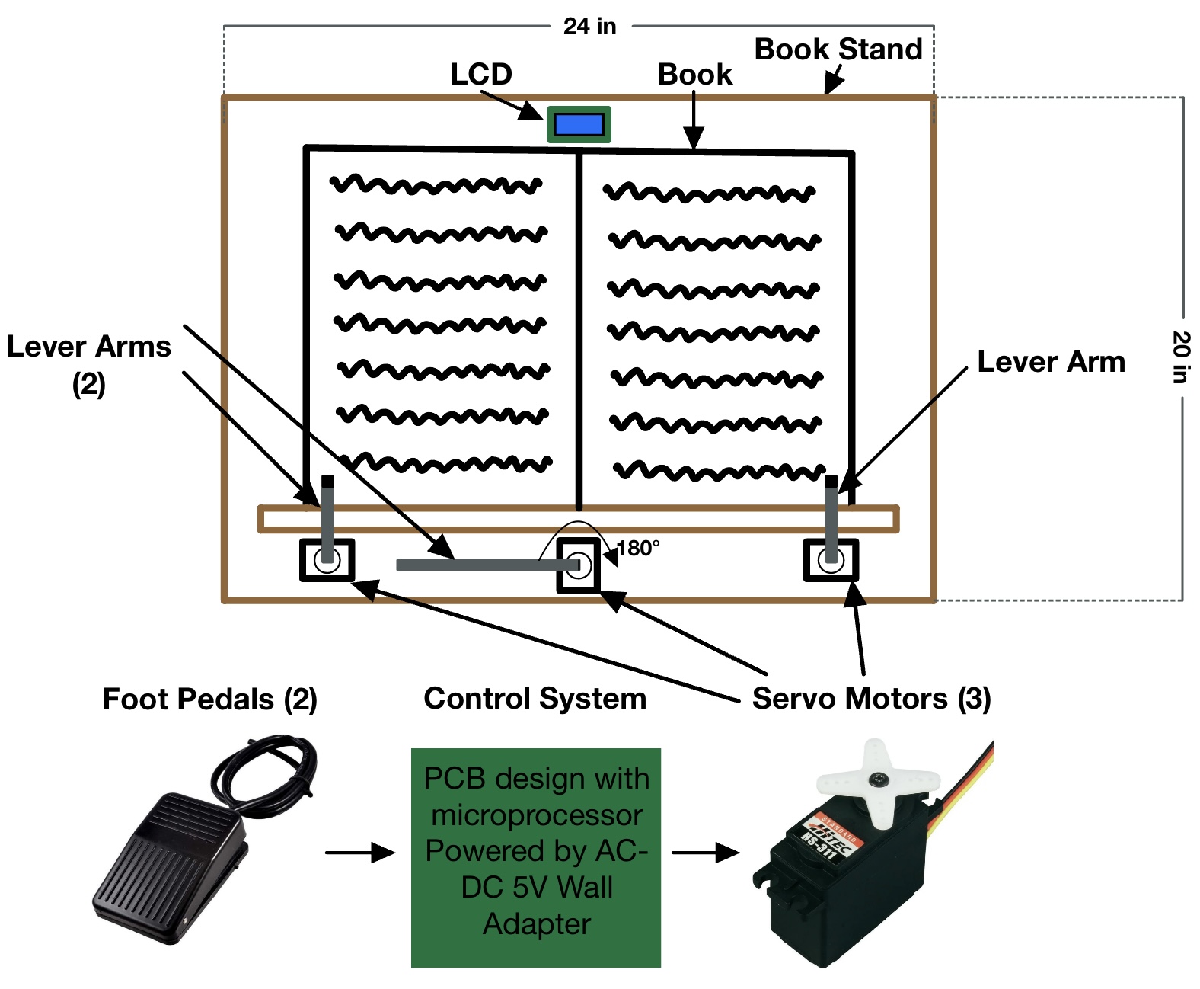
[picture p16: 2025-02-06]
Photos-Videos/Diagram.jpg

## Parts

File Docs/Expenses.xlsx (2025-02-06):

Item | Cost | Link | Person who purchased | Microcontroller - possibly from ECE supply store | Total | $165.44 | Javi | 88.8 | 40
Sheet Music Book | $14.17 | music book (https://www.amazon.com/Intermediate-Romantic-Era-Favorites-Collection/dp/1540089037?s=books) | Javi | AC Wall Adapter |  |  | Alyssa | 65
Sticky Tack | $5.86 | Sticky Tack (https://www.amazon.com/Amscan-34660-Sticky-Party-Favor/dp/B000HAZCS8?hvadid=309821945929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) | Javi | AC-DC Converter |  |  | Adia | 59.7 | 50
 |  |  |  | Voltage Regulator stuff |  |  | total | 213.5
2 medium/large motors |  |  |  | On/Off switch |  |  | Split 3 ways | 71.16666667
 |  |  |  | Headers for ISP and 3 pin on pcb
two way pedal | $20.86 | pedal (https://www.amazon.com/dp/B07KN6GLYD?psc=1&smid=A2ISRIWV0VLTC5&ref_=chk_typ_imgToDp) | Adia
3 motors (Hitec HS-311 Servo Standard Universal) | $44.00 |  | Alyssa
55 Wires Supply Center | $21.00 |  | Alyssa
2 microcontrollers | $15.00 | microcontroller (https://www.ebay.com/itm/255941311837) | Javi
isp programmer | $14.32
pcb order | $30.23 |  | Javi
3 microncontroller | $23.54 |  | Javi
Microntrollers | $24.52 |  | Adia
$5.89
$20.86
$44.28 |  | $8.89
$5.86 |  | $129.57
$30.00
$0.60
$1.65
$0.82
$1.44
$1.69
$2.80
$0.81
$6.27
$0.45
$2.46
$0.69
$3.00

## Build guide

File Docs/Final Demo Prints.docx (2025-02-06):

High-Level Requirements

For our solution to be considered successful, it must achieve the following three goals:

- The device must be able to turn one page within 5 seconds ± 2 seconds. This motion should be repeatable for turning a page backward.
- The device must be able to turn at least ten consecutive pages, with 95% ± 5% accuracy, and take at most 1 minute ± 10 seconds when the foot pedal is pressed consecutively.
- The device must be able to store the total number of pages turned in a single sitting, with 95% ± 5% accuracy, and display this information to the reader.

Block Diagram


Subsystem Testing

Power Subsystem

Requirements | Verification
- Must have a 5V wall adapter that plugs into a wall outlet. - All components on the PCB must be supplied with 5 V ± 5%, when the device is idle and active. | - Use a multimeter to check that the wall adapter’s barrel jack is supplying a steady 5V ± 5%. - Measure the voltage across each device using an oscilloscope. Repeat this process when a foot pedal is pressed.

Actuation Subsystem

Requirement | Verification
- The servo motors must create negligible backwards EMF. - The motors should cause minimal damage or tearing to the pages in the book. | - Use an oscilloscope to plot the voltage of a motor when idle and when active. If the voltage spike is 1V ± 0.5V, we can consider the backwards EMF from the motor to be negligible. - Run 10 test trials to find the best angle and speed for each motor.

Control and Sensor Subsystem

Requirements | Verification
- When the left foot pedal is pressed, the motors should turn a page backward. When the right foot pedal is pressed, the motors should turn a page forward. - The LCD should track the number of pages turned forward. | - Ensure that the left motor rotates 45°-135°-45° and the center motor rotates 0°-90°-180° when the left pedal is pressed. Ensure that the right motor rotates 135°-45°-135° and the center motor rotates 180°-90°-0° when the right pedal is pressed. - When the right foot pedal is pressed, the count should increase by 1. If the left foot pedal is pressed, the count should decrease by 1.

Software Flowchart

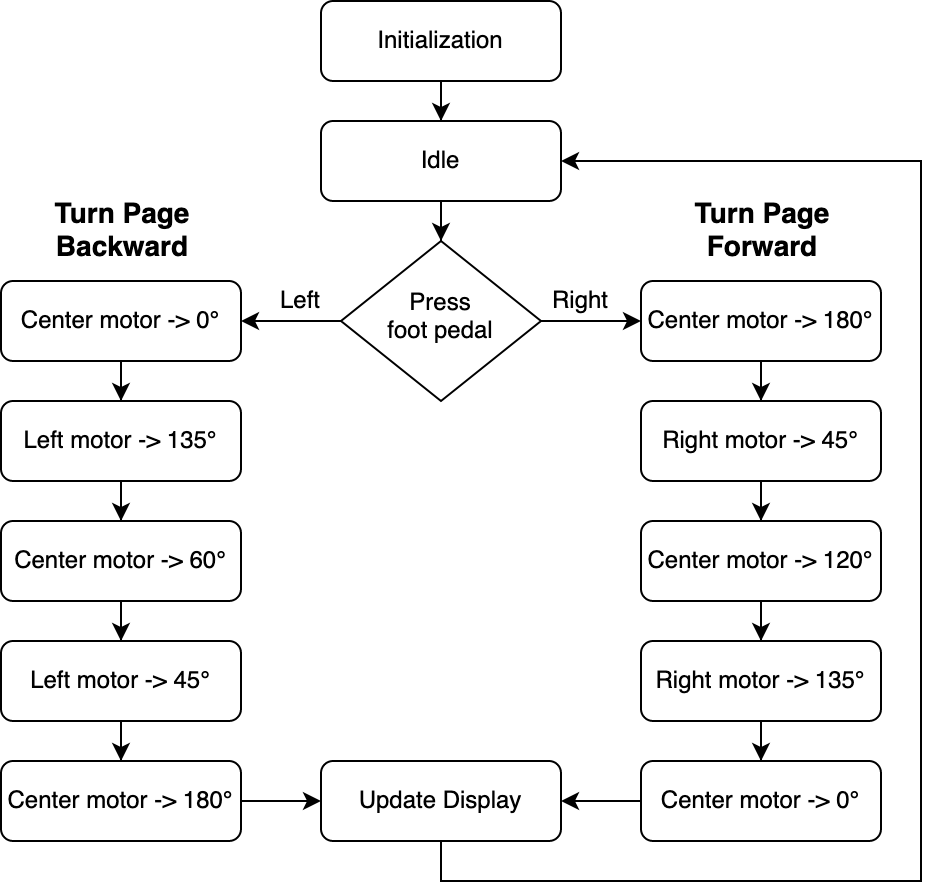
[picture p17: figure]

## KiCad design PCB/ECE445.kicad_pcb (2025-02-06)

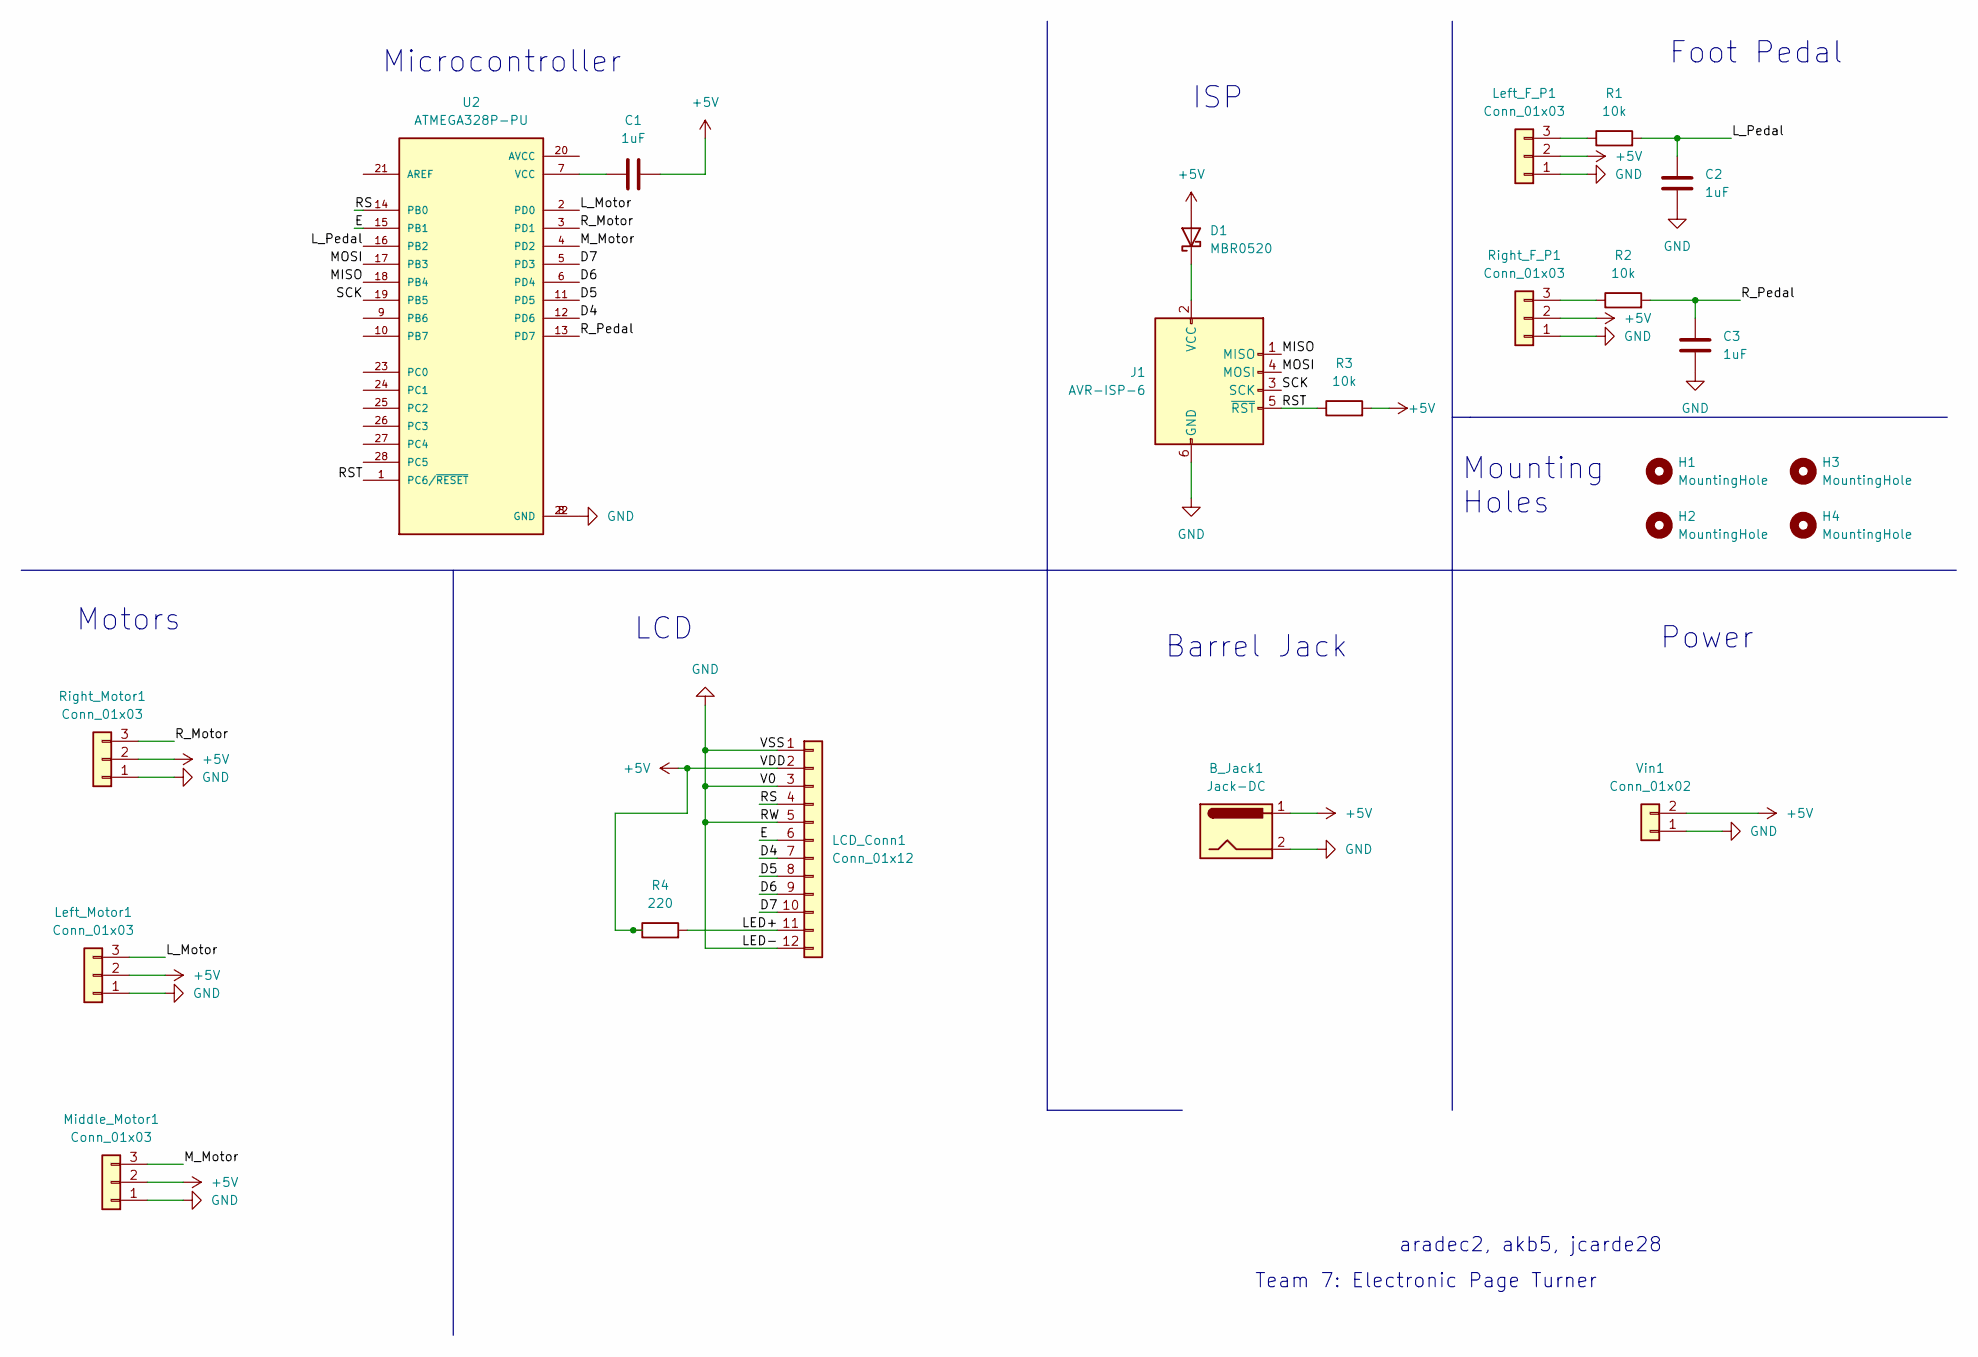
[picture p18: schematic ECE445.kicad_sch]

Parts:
B_Jack1: Jack-DC; BarrelJack_Horizontal
C1, C2, C3: 1uF; C_0805_2012Metric_Pad1.18x1.45mm_HandSolder
D1: MBR0520; D_SOD-123
H1, H2, H3, H4: MountingHole; MountingHole_3.2mm_M3
J1: AVR-ISP-6; IDC-Header_2x03_P2.54mm_Vertical
LCD_Conn1: Conn_01x12; Molex_KK-254_AE-6410-12A_1x12_P2.54mm_Vertical
Left_F_P1: Conn_01x03; Molex_KK-254_AE-6410-03A_1x03_P2.54mm_Vertical
Left_Motor1: Conn_01x03; Molex_KK-254_AE-6410-03A_1x03_P2.54mm_Vertical
Middle_Motor1: Conn_01x03; Molex_KK-254_AE-6410-03A_1x03_P2.54mm_Vertical
R1, R2, R3: 10k; R_0805_2012Metric_Pad1.20x1.40mm_HandSolder
R4: 220; R_0805_2012Metric_Pad1.20x1.40mm_HandSolder
Right_F_P1: Conn_01x03; Molex_KK-254_AE-6410-03A_1x03_P2.54mm_Vertical
Right_Motor1: Conn_01x03; Molex_KK-254_AE-6410-03A_1x03_P2.54mm_Vertical
U2: ATMEGA328P-PU; DIP794W46P254L2967H457Q28B
Vin1: Conn_01x02; Molex_KK-254_AE-6410-02A_1x02_P2.54mm_Vertical

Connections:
+5V: B_Jack1.1, C1.2, D1.2 (A), LCD_Conn1.2, Left_F_P1.2, Left_Motor1.2, Middle_Motor1.2, R3.2, R4.1, Right_F_P1.2, Right_Motor1.2, Vin1.2; also elsewhere on the board
/D4: LCD_Conn1.7, U2.12 (PD6)
/D5: LCD_Conn1.8, U2.11 (PD5)
/D6: LCD_Conn1.9, U2.6 (PD4)
/D7: LCD_Conn1.10, U2.5 (PD3)
/E: LCD_Conn1.6, U2.15 (PB1)
/LED+: LCD_Conn1.11, R4.2; also elsewhere on the board
/L_Motor: Left_Motor1.3, U2.2 (PD0)
/L_Pedal: C2.1, R1.2, U2.16 (PB2)
/MISO: J1.1 (MISO), U2.18 (PB4)
/MOSI: J1.4 (MOSI), U2.17 (PB3)
/M_Motor: Middle_Motor1.3, U2.4 (PD2)
/RS: LCD_Conn1.4, U2.14 (PB0)
/RST: J1.5 (~RST), R3.1, U2.1 (PC6/~RESET)
/R_Motor: Right_Motor1.3, U2.3 (PD1)
/R_Pedal: C3.1, R2.2, U2.13 (PD7)
/SCK: J1.3 (SCK), U2.19 (PB5)
GND: B_Jack1.2, C2.2, C3.2, J1.6 (GND), LCD_Conn1.1, LCD_Conn1.3, LCD_Conn1.5, LCD_Conn1.12, Left_F_P1.1, Left_Motor1.1, Middle_Motor1.1, Right_F_P1.1, Right_Motor1.1, U2.8 (GND), U2.22 (GND), Vin1.1
unnamed: C1.1, U2.7 (VCC)
unnamed: D1.1 (K), J1.2 (VCC)
unnamed: Left_F_P1.3, R1.1
unnamed: R2.1, Right_F_P1.3

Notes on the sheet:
ISP
Team 7: Electronic Page Turner
Mounting Holes
Microcontroller
aradec2, akb5, jcarde28
Power
Foot Pedal
LCD
Motors
Barrel Jack

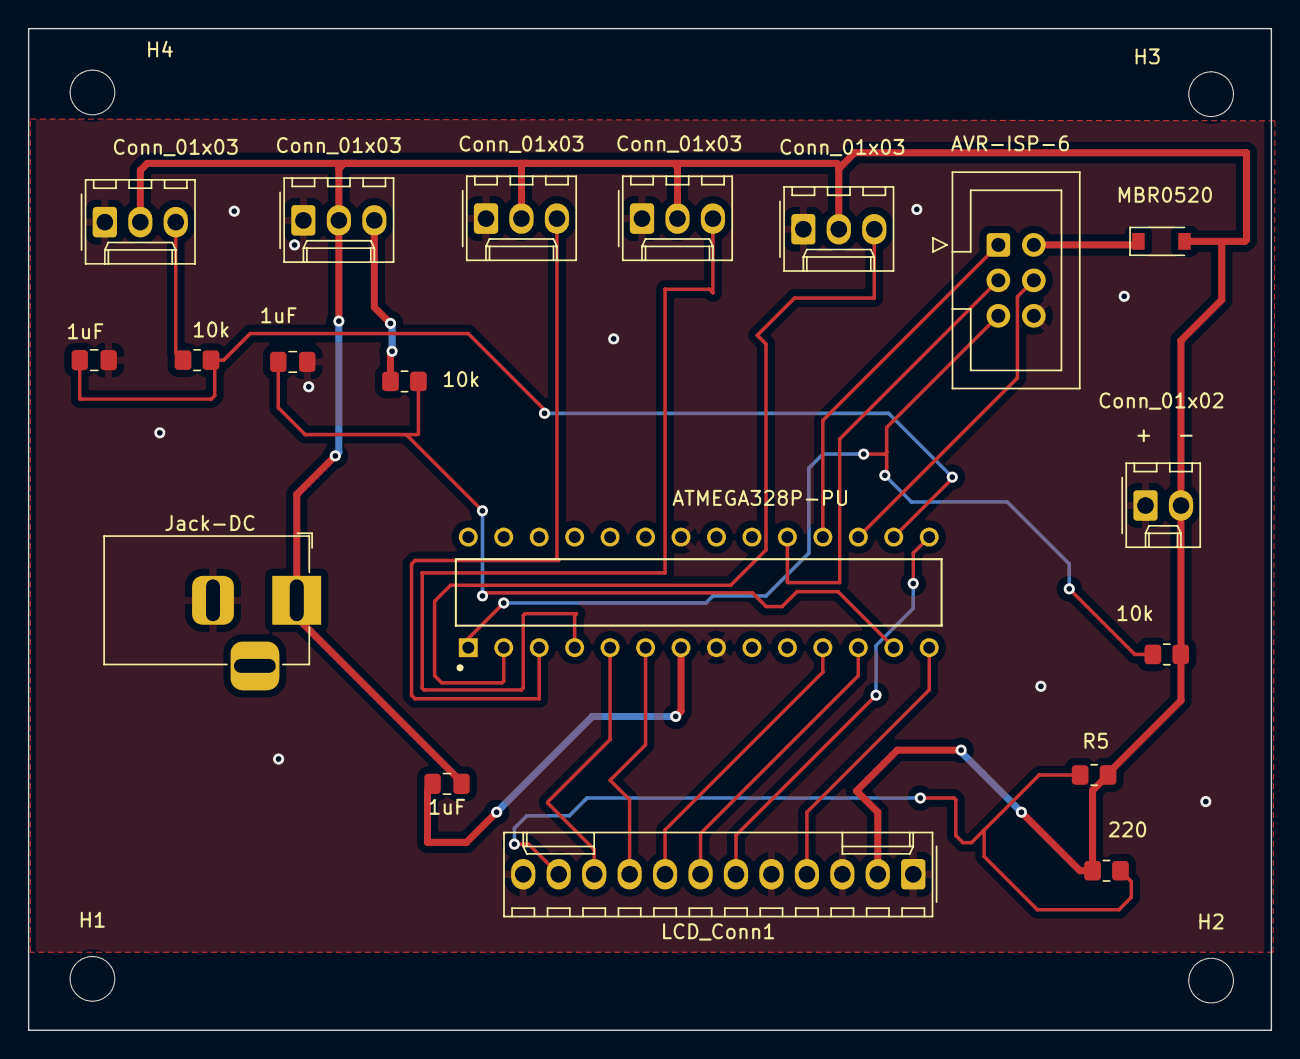
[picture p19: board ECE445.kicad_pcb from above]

Board: 2 copper layers, 89.0 x 71.8 mm, 23 parts (0 on the bottom side), 22 nets.

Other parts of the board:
R5: R5; R_0805_2012Metric_Pad1.20x1.40mm_HandSolder

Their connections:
+5V: R5.2; also elsewhere on the board
/LED+: R5.1; also elsewhere on the board

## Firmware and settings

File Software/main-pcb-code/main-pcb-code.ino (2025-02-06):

// code for main PCB - everything except the right motor
#include <Servo.h>
#include <LiquidCrystal.h>

// initialize the LCD library driver with the display pins connected to the arduino pins
const int rs = 8, en = 9, d4 = 6, d5 = 5, d6 = 4, d7 = 3;
LiquidCrystal lcd(rs, en, d4, d5, d6, d7);
  
// assign the switches connected to the arduino pins
const int right_switch_pin = 7;
const int left_switch_pin = 10;
int right_switch_state = 0;
int left_switch_state = 0;

// create the servo objects to control the left, center, and right servo motors
Servo left_servo;
Servo center_servo;
// Servo right_servo;
const int lservo_pin = 0;
const int cservo_pin = 2;

int pages_read = 0; // only keeps track of pages turned forward
int bookmark = 50; // this is where we are starting from
int display_flag = 0; // used to update display

void setup() {
  // LCD setup
  lcd.begin(16, 4); // set up of the LCD's number of columns and rows
  lcd.setCursor(0, 0);
  lcd.print("Turn Counter:");
  lcd.setCursor(0, 1);
  lcd.print("0 pages turned");
  lcd.setCursor(0, 3);
  lcd.print("Bookmark: Pg 50");

  // foot pedal switches setup
  pinMode(right_switch_pin, INPUT);
  pinMode(left_switch_pin, INPUT);

  // orientation setup for the motors (all set to 0 degrees)
  Serial.begin(9600); // send and receive at 9600 baud (needed to send data to the motors)
  left_servo.attach(lservo_pin); // attaches the left servo on pin 7 to the servo object
  left_servo.write(45);
  center_servo.attach(cservo_pin); // attaches the center servo on pin 6 to the servo object
  center_servo.write(0);
}

void loop() {
  // read the state of the foot pedal switches
  right_switch_state = digitalRead(right_switch_pin); 
  left_switch_state = digitalRead(left_switch_pin); 

  // check if the foot pedals were pressed
  if (left_switch_state==HIGH && right_switch_state==LOW) { // backwards turning code
    center_servo.write(0);
    delay(1000);
    left_servo.write(155);
    delay(1000);
    center_servo.write(60);
    delay(1000);
    left_servo.write(45);
    delay(1000);
    center_servo.write(165);
    pages_read--; // decrement pages read
    bookmark--;
    display_flag = 1;
  }

  if (left_switch_state==LOW && right_switch_state==HIGH) { // forwards turning code
    center_servo.write(165);
    delay(2000);
    // right_servo.write(25);
    // delay(1000);
    center_servo.write(120);
    delay(2000);
    // right_servo.write(145);
    // delay(1250);
    center_servo.write(0);
    pages_read++; // increment pages read
    bookmark++;
    display_flag = 1;
  }  

  // update display
  if (display_flag == 1) {
    lcd.setCursor(0, 1);
    if (pages_read == 1) {
      lcd.print("                "); // clear the row
      lcd.setCursor(0, 1);
      lcd.print("1 page forward");
    }
    else if (pages_read == -1) {
      lcd.print("                "); // clear the row
      lcd.setCursor(0, 1);
      lcd.print("1 page backward");
    }
    else if (pages_read > 1) {
      lcd.print("                "); // clear the row
      lcd.setCursor(0, 1);
      lcd.print(pages_read); // constantly display the page count (never negative)
      lcd.print(" pages forward");
    }
    else if (pages_read < -1) {
      lcd.print("                "); // clear the row
      lcd.setCursor(0, 1);
      lcd.print(abs(pages_read)); // constantly display the page count (never negative)
      lcd.print(" pages backward");
    }
    else {
      lcd.print("                "); // clear the row
      lcd.setCursor(0, 1);
      lcd.print("0 pages turned");
    }
    lcd.setCursor(0, 3);
    lcd.print("                "); // clear the row
    lcd.setCursor(0, 3);
    lcd.print("Bookmark: Pg ");
    lcd.print(bookmark);
    display_flag = 0;
  }
}

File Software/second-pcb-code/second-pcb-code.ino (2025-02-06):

#include <Servo.h>

// assign the switches connected to the arduino pins
const int right_switch_pin = 7;
int right_switch_state = 0;

// create the servo objects to control the right servo motors
Servo right_servo;
const int rservo_pin = 2;

void setup() {
  // put your setup code here, to run once:

  // foot pedal switches setup
  pinMode(right_switch_pin, INPUT);

  // orientation setup for the motors (all set to 0 degrees)
  Serial.begin(9600); // send and receive at 9600 baud (needed to send data to the motors)
  right_servo.attach(rservo_pin); // attaches the right servo on pin 5 to the servo object
  right_servo.write(145);
}

void loop() {
  // put your main code here, to run repeatedly:
  right_switch_state = digitalRead(right_switch_pin); 

  if (right_switch_state==HIGH) { // forwards turning code
    delay(1250);
    right_servo.write(25);
    delay(2000);
    right_servo.write(145);
    delay(1000);
  }  
}

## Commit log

2025-02-06 added .gitignore
    [Agenda.xlsx, ECE445.kicad_pcb, ECE445.kicad_sch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]
2025-02-06 updated docs
    [Agenda.xlsx, Expenses.xlsx]
